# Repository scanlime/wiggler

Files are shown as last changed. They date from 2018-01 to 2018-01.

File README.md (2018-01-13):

Pen Wiggler 💃✒️
================

It's the worst drawing robot! Or perhaps the best, if simplicity is your favorite vice.

Work in progress...
Tutorial coming up soon.

- Runs on a Raspberry Pi (2 or 3)
- Draws with a felt tip pen, or maybe other things!
- Uses a Huion H610 or similar drawing tablet for feedback
- Coil emulates a tablet pen (with hardware PWM)
- Three vibration motors wiggle the pen (with software PWM)

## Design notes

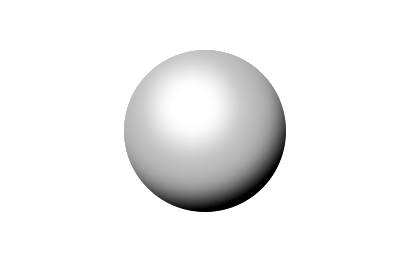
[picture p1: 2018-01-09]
images/shadecirc.png

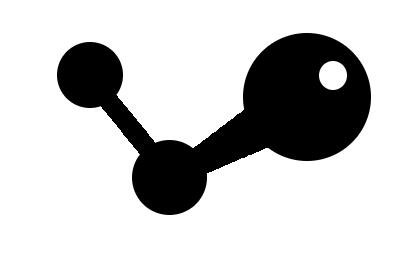
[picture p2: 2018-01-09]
images/circles.png

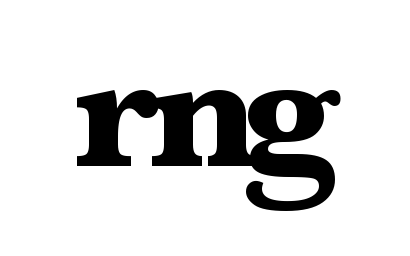
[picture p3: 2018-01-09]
images/rng2.png

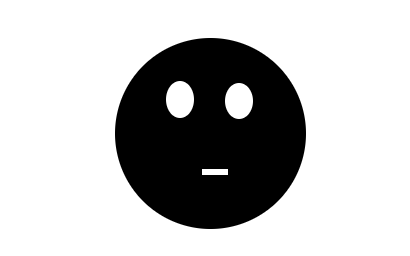
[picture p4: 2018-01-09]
images/facething.png

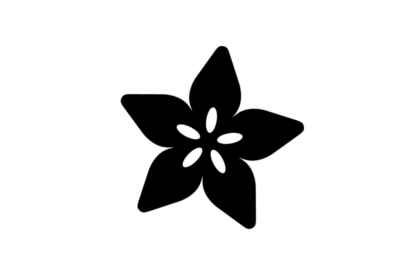
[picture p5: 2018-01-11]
images/adafruit.png

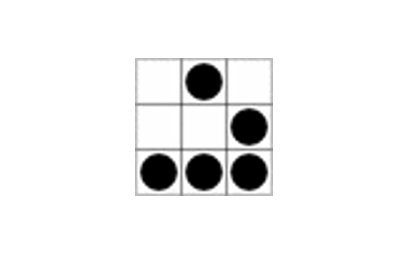
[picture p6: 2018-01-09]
images/glider.png

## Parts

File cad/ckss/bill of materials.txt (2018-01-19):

spring metal: berillium bronze C17200, 0.2mm
non-spring metal: brass, 0.2mm
birch plywood, 3.6mm
nuts and bolts M2

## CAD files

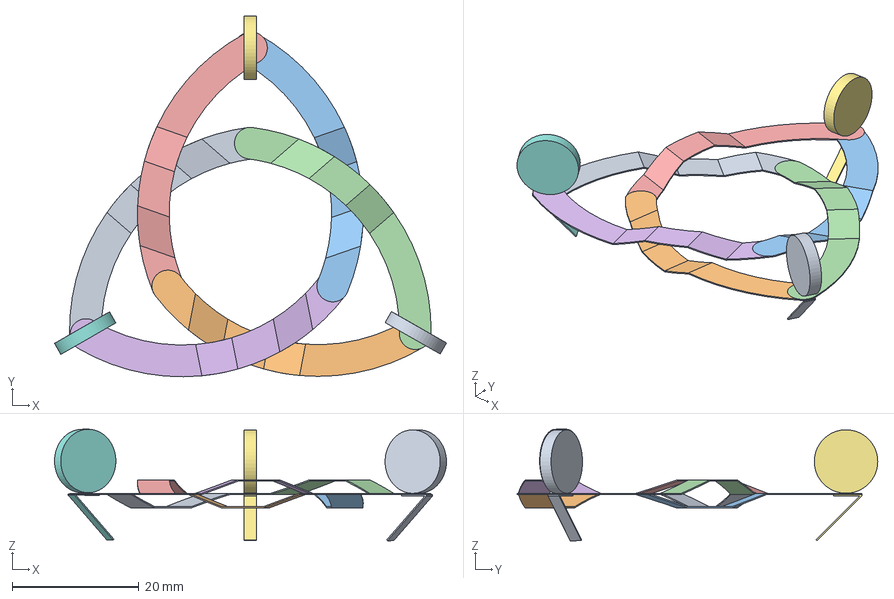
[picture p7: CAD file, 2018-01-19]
cad/ckss/celtic knot suspension system.fcstd
61.8 x 56.8 x 17.6 mm

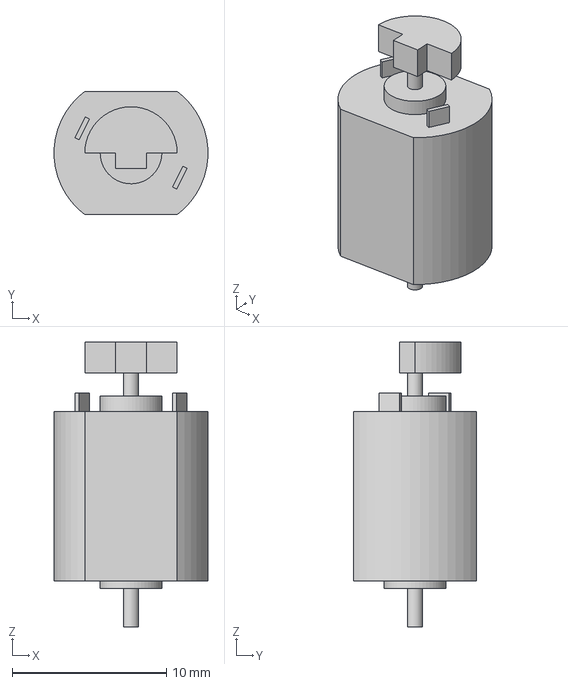
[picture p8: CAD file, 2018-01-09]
cad/flexy-v1/Vibe Motor v4.step
9.98 x 8.00 x 18.5 mm

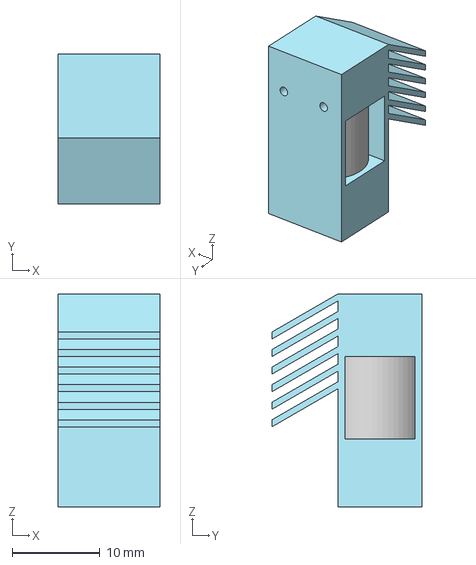
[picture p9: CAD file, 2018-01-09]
cad/flexy-v1/Vibro Leg v5.step
11.6 x 17.1 x 24.3 mm

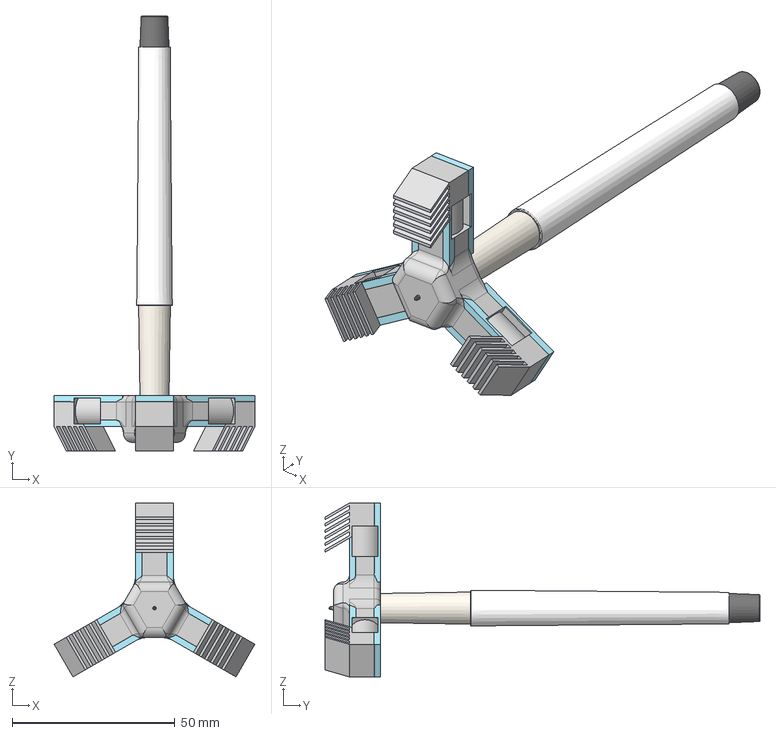
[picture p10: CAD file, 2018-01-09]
cad/flexy-v1/Bot Body v3.step
61.7 x 133.8 x 53.5 mm
Sharpie v1
Vibe Motor v4 x 3

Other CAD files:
cad/flexy-v1/Bot Body v3.f3d
cad/flexy-v1/Bot Body v3.stl
cad/flexy-v1/Vibe Motor v4.f3d

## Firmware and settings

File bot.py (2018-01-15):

#!/usr/bin/env python3

import time, random, math, sys, queue
import subprocess, collections, multiprocessing
import pygame, pigpio, evdev, numpy
from PIL import Image, ImageOps, ImageMath, ImageFilter, ImageDraw


class WiggleBot:
    """Controls the robot motors and reads sensors, navigating based on a goal map.
       Runs in a separate process which tries to stay in sync with the tablet event rate.
       """

    minimum_speed = 0.04
    velocity_smoothing = 0.94
    pwm_initial_startup = 0.25
    pwm_initial_increment = 0
    pwm_initial_decay = 0
    pwm_acceleration = 1.012
    ray_samples = 32
    ray_length = 0.7
    ray_shape_exponent = 6.0
    ray_edge_penalty = 0.1
    ray_sample_bias = 96
    ray_sample_exponent = 2.0
    mode_revisit_period = 3.0
    minimum_mode_duration = 0.25

    mode_pwm = [
        (1, 0, 0),
        (0, 1, 0),
        (0, 0, 1),
        (0, 1, 1),
        (1, 0, 1),
        (1, 1, 0),
    ]

    def __init__(self):
        self.state = WiggleState(self.mode_pwm, self.pwm_initial_startup)

    def start(self):
        self.goal_queue = multiprocessing.Queue(2)
        self.state_rx, self.state_tx = multiprocessing.Pipe(False)
        self.process = multiprocessing.Process(target=self._proc)
        self.process.start()

    def _proc(self):
        # Motor control process

        self.goal = None
        self.pi = pigpio.pi()
        self.tablet = TabletLoop(self.pi)
        self.motors = Motors(self.pi)

        try:
            while True:
                self.step()
        finally:
            self.shutdown()
            
    def shutdown(self):
        # self.pi might be locked
        pi = pigpio.pi()
        Motors(pi).off()
        TabletTx(pi).off()

    def step(self):
        # Main control loop is driven by tablet event timing; wait for a HID report
        self.tablet.read()
        position = self.tablet.rx.scaled_pos()
        timestamp = self.tablet.rx.timestamp

        # Update instantaneous position and velocity
        if self.state.position is not None:
            dt = timestamp - self.state.timestamp
            diff = position - self.state.position
            if dt > 0 and diff[0] != 0.0 and diff[1] != 0.0:
                hist = self.state.dt_histogram
                hist[min(len(hist)-1, int(dt * 2000))] += 1
                self.state.velocity = diff / dt
        self.state.position = position
        self.state.timestamp = timestamp
        self.state.frame_counter = self.tablet.frame_counter

        # If we haven't desynchronized recently and the tablet was in the same mode
        # at each end of this step, update the mode-specific smoothed velocity estimate.
        if (self.state.current_mode is not None
            and self.state.last_mode == self.state.current_mode
            and self.state.velocity is not None and self.tablet.is_synchronized()):
            mode = self.state.modes[self.state.current_mode]
            mode.timestamp = self.state.timestamp
            mode.update_velocity(self.state.velocity, self.velocity_smoothing)
            if mode.timestamp - self.state.mode_change_timestamp > self.minimum_mode_duration:
                self.update_initial_pwm(mode.velocity)
        self.state.last_mode = self.state.current_mode

        # Share the latest state
        self.state_tx.send(self.state)

        # Get the latest goal map
        try:
            while True:
                self.goal = self.goal_queue.get_nowait()
        except queue.Empty:
            pass

        # Change states maybe
        next_mode = self.choose_mode()
        if next_mode == self.state.current_mode:
            self.accelerate()
        else:
            self.set_mode(next_mode)

    def accelerate(self):
        self.motors.set([min(1.0, s * self.pwm_acceleration) for s in self.motors.speeds])

    def update_initial_pwm(self, velocity):
        # Adjust minimum PWM value to maintain minimum speed.
        # Called with smoothed velocity after a mode is old enough to switch.
        
        if velocity.dot(velocity) < self.minimum_speed * self.minimum_speed:
            self.increase_minimum_pwm()
        else:
            self.state.pwm_initial = max(0.0, self.state.pwm_initial - self.pwm_initial_decay)

    def increase_minimum_pwm(self):
        self.state.pwm_initial = min(1.0, self.state.pwm_initial + self.pwm_initial_increment)
        self.set_to_minimum_pwm()

    def set_to_minimum_pwm(self):
        if self.state.current_mode is not None:
            pwm = self.state.modes[self.state.current_mode].pwm
            self.motors.set([p * self.state.pwm_initial for p in pwm])

    def set_mode(self, mode):
        self.state.current_mode = mode
        self.state.mode_change_timestamp = self.state.timestamp
        self.tablet.desync()
        self.set_to_minimum_pwm()

    def choose_mode(self):
        self.state.ray_debug_info = []

        # Keep the current mode if it's too soon to change
        if self.state.timestamp - self.state.mode_change_timestamp < self.minimum_mode_duration:
            return self.state.current_mode

        # Refresh modes with old velocity estimates, starting with the oldest
        modes = self.state.modes
        oldest_mode = 0
        for i, mode in enumerate(modes):
            if mode.timestamp < modes[oldest_mode].timestamp:
                oldest_mode = i
        if self.state.timestamp - modes[oldest_mode].timestamp > self.mode_revisit_period:
            return oldest_mode

        # Evaluate rays to find the best choice
        scores = []
        best_mode = 0
        for mode in modes:
            ray_info = self.evaluate_ray(mode.velocity)
            self.state.ray_debug_info.append(ray_info)
            scores.append(ray_info[0])
        for i, score in enumerate(scores):
            if score > scores[best_mode]:
                best_mode = i
        return best_mode

    def evaluate_ray(self, vec):
        goal = self.goal
        if goal is None:
            return (0, dict(error='no_goal_yet'))
        position = self.state.position
        if position is None:
            return (0, dict(error='no_position_yet'))
        if vec is None:
            return (0, dict(error='no_input_yet'))
        norm = numpy.linalg.norm(vec)
        if norm <= 0.0:
            return (0, dict(error='input_vec_zero'))

        height, width = self.goal.shape
        major_axis = numpy.max(self.goal.shape)

        origin = major_axis * position
        direction = vec / norm
        ray_length = major_axis * self.ray_length
        sample_locs = numpy.arange(0,1,1/self.ray_samples).reshape((-1,1)) ** self.ray_shape_exponent
        points = numpy.round(origin + sample_locs * (ray_length * direction)).astype(int)
        clipped = numpy.clip(points, (0,0), (width-1, height-1))
        samples = self.ray_sample_bias + goal[clipped[:,1], clipped[:,0]] ** self.ray_sample_exponent
        total = numpy.linalg.norm(samples)
        edge_penalty = numpy.linalg.norm(clipped - points)
        score = total - edge_penalty * self.ray_edge_penalty
        return (score, dict(clipped_points=clipped))


class WiggleMode:
    """One vibration mode (a set of motors we expect to move the bot in a particular way)"""

    def __init__(self, pwm):
        self.pwm = pwm
        self.velocity = numpy.array((0,0))
        self.timestamp = 0

    def update_velocity(self, vec, smoothing):
        self.velocity = self.velocity * smoothing + numpy.array(vec) * (1-smoothing)
    

class WiggleState:
    """Current state of the bot controller, saved on every timestep"""

    def __init__(self, mode_pwm, pwm_initial):
        self.timestamp = None
        self.position = None
        self.velocity = None
        self.pwm_initial = pwm_initial
        self.ray_debug_info = []
        self.current_mode = None
        self.last_mode = None
        self.mode_change_timestamp = 0
        self.modes = [WiggleMode(p) for p in mode_pwm]
        self.frame_counter = 0
        self.dt_histogram = [0] * 20

    def __repr__(self):
        return "<frame %06d, pos=%s, mode=%s pwmi=%.6f dthist=%s>" % (
            self.frame_counter, self.position, self.current_mode, self.pwm_initial, self.dt_histogram)


class GreatArtist:
    """Image-based algorithms for goal determination and status output.
       The generated goal images are sent to the WiggleBot asynchronously.
       """
       
    frame_delay = 0.5

    def __init__(self, inspiration):
        self.bot = WiggleBot()
        self.display = Display()
        self.movie = VideoEncoder()

        self.inspiration = ImageOps.invert(Image.open(inspiration).convert('L'))
        self.progress = Image.new('L', self.inspiration.size, 0)
        self.debugview = Image.new('L', self.inspiration.size, 0)
        self.progress_draw = ImageDraw.Draw(self.progress)
        self.debugview_draw = ImageDraw.Draw(self.debugview)

        self.major_axis = max(*self.inspiration.size)
        self.large_blur = ImageFilter.GaussianBlur(32)

        self.frame_counter = 0
        self.goal = None
        self.goal_timestamp = None
        self.mode_scores = None
        self.step_timestamp = None

    def run(self):
        movie_file = time.strftime('bot-%y%m%d-%H%M%S.mp4', time.localtime())
        self.movie.start(movie_file, self.inspiration.size)
        self.display.start(self.inspiration.size)
        self.bot.start()
        while True:
            self.step()

    def step(self):
        # Compute and send a new goal image
        sub = ImageMath.eval("convert(i - prog/2, 'L')", dict(i=self.inspiration, prog=self.progress))
        self.goal = ImageMath.eval("convert(a/2+b, 'L')", dict(a=sub, b=sub.filter(self.large_blur)))
        self.bot.goal_queue.put(numpy.asarray(self.goal))

        # Drain the queue of incoming states from the bot control process
        while self.bot.state_rx.poll():
            prev_pos = self.bot.state.position
            self.bot.state = self.bot.state_rx.recv()
            self.record_bot_travel(prev_pos, self.bot.state.position)
            self.draw_per_state_debug()

        # Update the output images
        self.draw_debug_latest_position()
        status_im = Image.merge('RGB', (self.debugview, self.goal, ImageOps.invert(self.progress)))
        self.display.show(status_im)
        self.movie.encode(status_im)

        self.frame_counter += 1
        self.debugview.paste(im=0, box=(0, 0,)+self.debugview.size)

        print("[%06d] %r" % (self.frame_counter, self.bot.state))
        time.sleep(self.frame_delay)

    def record_bot_travel(self, from_pos, to_pos, distance_threshold=0.1):
        if from_pos is None or to_pos is None:
            return
        dist = to_pos - from_pos
        if dist.dot(dist) > distance_threshold * distance_threshold:
            # Ignore large jumps
            return

        s = self.major_axis
        self.progress_draw.line((s*from_pos[0], s*from_pos[1],
            s*to_pos[0], s*to_pos[1]), fill=255, width=1)

    def draw_per_state_debug(self):
        modes = self.bot.state.modes
        current = self.bot.state.current_mode 

        for mode in modes:
            # Follow the bot with all available vectors
            self.draw_vibration_mode_line(mode, self.bot.state.position)

        if current is not None:
            # Oscilloscope trace for current mode
            w, h = self.debugview.size
            frame_x = self.bot.state.frame_counter % w
            self.debugview.paste(im=255, box=(frame_x, current*4, frame_x+1, (current+1)*4))

            # Oscilloscope trace for vectors; X is time, Y is mode
            grid = ((0.004 * self.bot.state.frame_counter) % 1.0, (2+current) * 0.05)
            self.draw_vibration_mode_line(modes[current], grid)

        # Per-ray debugging from this state
        for score, ray_info in self.bot.state.ray_debug_info:
            for pt in ray_info.get('clipped_points', []):
                self.debugview.putpixel(pt, 180)

    def draw_debug_latest_position(self):
        pos = self.bot.state.position
        if pos is not None:
            s = self.major_axis
            width, height = self.debugview.size
            self.debugview.paste(im=255, box=(0, int(s*pos[1]), width, int(s*pos[1])+1))
            self.debugview.paste(im=255, box=(int(s*pos[0]), 0, int(s*pos[0])+1, height))

    def draw_vibration_mode_line(self, mode, from_pos, zoom=2.0, width=1):
        s = max(*self.debugview.size)
        if from_pos is not None and mode.velocity is not None:
            to_pos = (from_pos[0] + mode.velocity[0]*zoom, from_pos[1] + mode.velocity[1]*zoom)
            ipos = (int(s*from_pos[0]), int(s*from_pos[1]))
            self.debugview_draw.line((s*from_pos[0], s*from_pos[1], s*to_pos[0], s*to_pos[1]), fill=255, width=width)


class Motors:
    def __init__(self, pi, hz=200):
        self.pi = pi
        self.pins = (23, 24, 25)
        self.count = len(self.pins)
        for pin in self.pins:
            self.pi.set_PWM_frequency(pin, hz)

    def set(self, speeds):
        self.speeds = tuple(speeds)
        for speed, pin in zip(self.speeds, self.pins):
            self.pi.set_PWM_dutycycle(pin, max(0, min(255, int(255 * speed))))

    def off(self):
        self.set((0,) * self.count)


class TabletLoop:
    def __init__(self, pi):
        self.tx = TabletTx(pi)
        self.rx = TabletRx()
        self.toggle = False
        self.frame_counter = 0
        self.update_pressure()

    def read(self):
        self.rx.sync_read()
        self.frame_counter = self.frame_counter + 1
        self.update_pressure()

    def desync(self):
        if self.is_synchronized(): 
            self.toggle = not self.toggle
            self.update_pressure()

    def is_synchronized(self):
        return (self.rx.get_pressure() > 0.3) == self.toggle

    def update_pressure(self):
        anti_idleness_ramp = (self.frame_counter & 7) / 7 - 0.5
        self.tx.set_pressure(0.1 + 0.7 * float(self.toggle) + 0.05 * anti_idleness_ramp)


class TabletTx:
    idle_hz = 255000

    def __init__(self, pi):
        self.pi = pi

    def set_pressure(self, p):
        self.set_hz(int(self.idle_hz + max(0.0, min(1.0, p)) * 9000))

    def set_hz(self, hz, duty=0.1):
        self.pi.hardware_PWM(18, hz, int(1e6 * duty))

    def off(self):
        self.set_hz(self.idle_hz, 0)


class TabletRx:
    """Receive low-level tablet events via the Linux Event subsystem"""

    def __init__(self):
        ABS = evdev.ecodes.EV_ABS
        X, Y, P = evdev.ecodes.ABS_X, evdev.ecodes.ABS_Y, evdev.ecodes.ABS_PRESSURE
        for path in evdev.list_devices():
            dev = evdev.InputDevice(path)
            caps = dev.capabilities()
            if ABS not in caps:
                continue
            ab = dict(caps[ABS])
            if X in ab and Y in ab and P in ab:
                self.x, self.y, self.p = (ab[X], ab[Y], ab[P])
                self.timestamp = 0
                self.dev = dev
                print("Using device as tablet:", dev)
                dev.grab()
                return
        raise IOError("Couldn't find the tablet (looking for an input device with X, Y, and Pressure)")

    def sync_read(self):
        SYN, ABS = evdev.ecodes.EV_SYN, evdev.ecodes.EV_ABS
        X, Y, P = evdev.ecodes.ABS_X, evdev.ecodes.ABS_Y, evdev.ecodes.ABS_PRESSURE
        for ev in self.dev.read_loop():
            if ev.type == SYN:
                self.timestamp = ev.timestamp()
                break
            if ev.type == ABS:
                if ev.code == X: self.x = self.x._replace(value=ev.value)
                if ev.code == Y: self.y = self.y._replace(value=ev.value)
                if ev.code == P: self.p = self.p._replace(value=ev.value)

    def scaled_pos(self):
        s = 1.0 / max(self.x.max - self.x.min, self.y.max - self.y.min)
        return numpy.array((s * (self.x.value - self.x.min), s * (self.y.value - self.y.min)))

    def get_pressure(self):
        return (self.p.value - self.p.min) / (self.p.max - self.p.min)


class Display:
    zoom = 2

    def start(self, size):
        self.size = numpy.array(size)
        self.queue = multiprocessing.Queue(2)
        self.process = multiprocessing.Process(target=self._proc)
        self.process.start()

    def show(self, img):
        try:
            self.queue.put_nowait(img.tobytes())
        except queue.Full:
            pass

    def _proc(self):
        screen = pygame.display.set_mode(self.size * self.zoom)
        pygame.display.set_caption('Wiggle Bot')
        while True:
            surf = pygame.image.fromstring(self.queue.get(), self.size, 'RGB')
            pygame.transform.scale(surf.convert(screen), screen.get_size(), screen)
            pygame.display.update()


class VideoEncoder:
    def start(self, filename, size, fps=30, crf=15, zoom=2, vid_size=(1280,720)):
        self.filename = filename
        self.fps = fps
        self.crf = crf
        self.size = size
        vf_scale = 'scale=%dx%d:flags=neighbor' % (size[0]*zoom, size[1]*zoom)
        vf_pad = 'pad=%d:%d:(ow-iw)/2:(oh-ih)/2' % vid_size
        filters = (vf_scale, vf_pad)
        self.proc = subprocess.Popen([
            'ffmpeg', '-y', '-pix_fmt', 'rgb24', '-f', 'rawvideo',
            '-s', '%dx%d' % self.size, '-r', str(self.fps),
            '-i', '-', '-crf', str(self.crf),
            '-vf', ','.join(filters), self.filename],
            stdin=subprocess.PIPE)

    def encode(self, img):
        self.proc.stdin.write(img.tobytes())


if __name__ == "__main__":
    if len(sys.argv) == 2:
        GreatArtist(sys.argv[1]).run()
    else:
        sys.stderr.write('usage: %s <image file>\n' % sys.argv[0])

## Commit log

2018-01-09 Original CAD files from July 2016
    [Bot Body v3.f3d, Bot Body v3.step, Bot Body v3.stl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]
2018-01-09 Maybe the version from the first "rng"
    My version control has been sloppy so far,
    but I think this is the script that produced the
    first intelligible "rng" drawing.
    - does converge well on the provided shape
    - prone to getting lost outside the shape often
    - not good at staying inside the lines
    - relatively fast
    [bot.py]
2018-01-11 oops, that was too fast
    [bot.py]
2018-01-11 Fewer better samples, less lag
2018-01-11 Samples were too far apart
2018-01-11 PWM feedback to keep the slow speed slow
2018-01-12 Tweak ratio of inspiration to progress, less holes in the paper
2018-01-12 Faster min speed, shorter ray weights
    [bot.py]
2018-01-12 Wide lines suck, try a short blur
    [bot.py]
2018-01-12 New debug style for velocity vectors
2018-01-12 Include vibe modes for motor pairs too
2018-01-13 Bias was too low to overcome blur background noise
    [bot.py]
2018-01-13 Ray debugging, more jitter
    [bot.py]
2018-01-13 Tiny bugfix in initial mode
    [bot.py]
2018-01-14 Experimenting with more vibration modes
    [bot.py]
2018-01-14 New bot control loop in a separate subprocess
    This should be much faster, but still needs more
    debugging, and is currently a bit less debuggable.
    One subprocess tries to stay in sync with the tablet
    event rate, and updates the motors. It uses queues to
    accept updated goal images and deliver status updates
    to another process, which does the slower image operations.
2018-01-15 Fixes for shutdown and frame dropping
    [bot.py]
2018-01-19 celtic knot suspension system
    [celtic knot suspension system.fcstd]
2018-01-19 Move v1 prototype to subdir
    [Bot Body v3.f3d, Bot Body v3.step, Bot Body v3.stl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]
